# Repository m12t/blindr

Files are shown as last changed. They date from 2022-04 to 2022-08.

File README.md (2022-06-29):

# blindr
An embedded systems project that automates the articulation of window blinds such that they automatically open at sunrise and close at sunset each day.

## About the Project
The goal for this project is to have window blinds that automatically open and close around sunrise and sunset in an effort to instill healthy a sleep pattern. The code is written in C using the C/C++ SDK for the Raspberry Pi Pico microcontroller board.

The name `blindr` was a joke on the joke from this hilarious video by Joma Tech on [if Apple made window blinds...](https://youtu.be/Hv6EMd8dlQk).

## Features
1. Fully motorized articulation of blind slats
1. A generic code architecture that can be used by anyone, anywhere on Earth, without modification (_granted you use the same components found below_)
1. No bluetooth or WiFi needed -- a fully isolated and contained system
1. The ability to source latitude and longitude (needed for the solar calculations) and precise datetime data from a GNSS module
1. The ability to enable and disable automation while still being able to "manually" control the blinds via a 3 position toggle switch

## High Level Code Overview
Being an embedded system that will run 24/7, reliability and low power consumption were identified as mission-critical parameters from the project's inception.
Some examples of this in action:
1. The stepper and stepper driver board are put to sleep (no current flows to the motor or driver charge pump) whenever it's not actively running
1. The main processing cores sleep indefinitely only to be woken up by toggle switch interrupts and RTC-based alarms for solar events
1. The GNSS module is put in low power mode when it isn't needed

## User Interface
The only direct input the user has with the system is through the 3 position toggle switch. Once powered on, the Pico will wait for toggle pin input that will be used to detect the boundaries of the blinds (fully closed up and fully closed down). It's critical that the first input in either direction (the order doesn't matter) goes all the way to the desired boundary. Once low and high boundaries are set, the toggle pin can be used to control the position of the blinds "manually". The code keeps track of the position of the blinds at all times and will not let the blinds turn past the given boundaries. To disable automation and keep the blinds shut indefinitely, leave the toggle switch flipped up or down which will move to the specified boundary, sleep the stepper, and wait for the toggle to be reset to the neutral position to enable automation again. There is currently no way to leave the blinds open and disable automation without unplugging the unit. This functionality could be encoded in a switch pattern such as `[up] [down] [up]` within a specified time frame, but leaving the blinds indefinitely open wasn't nearly as useful as being able to leave them indefinitely closed.

## Hardware
There are CAD and STL files for the stepper motor housing and a driveshaft (shown below) that I drafted up for this project. They will work if you happen to have the exact model of stepper (Shinano Kenshi STP-42D201-37 with 14 tooth gear) and blinds (Home Depot Home Decorators Collection) as me. I 3D printed the mount and driveshaft in PLA, though you will likely have to design your own or find another method of getting your stepper to actually turn your blinds. There is also a housing for the Pico uC and Big Easy Driver (also shown below). This repo focuses on the code, however, which _is_ compatable with any bipolar stepper and any mounting system you might use.

Stepper housing and drive shaft:
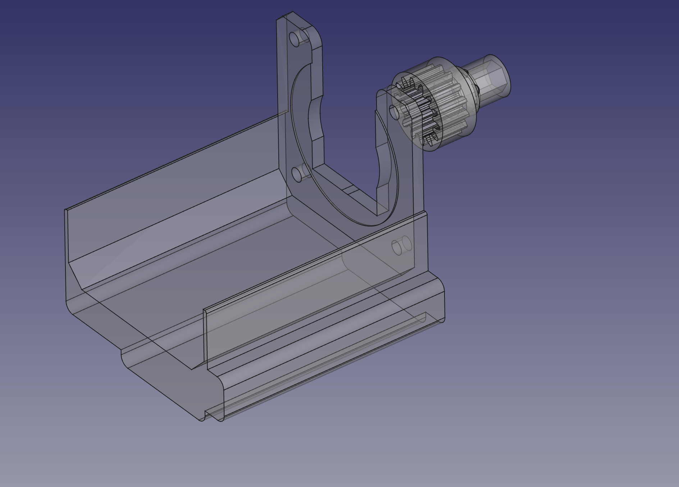
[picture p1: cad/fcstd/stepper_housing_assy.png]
Stepper housing and drive shaft


Case for the electronics:
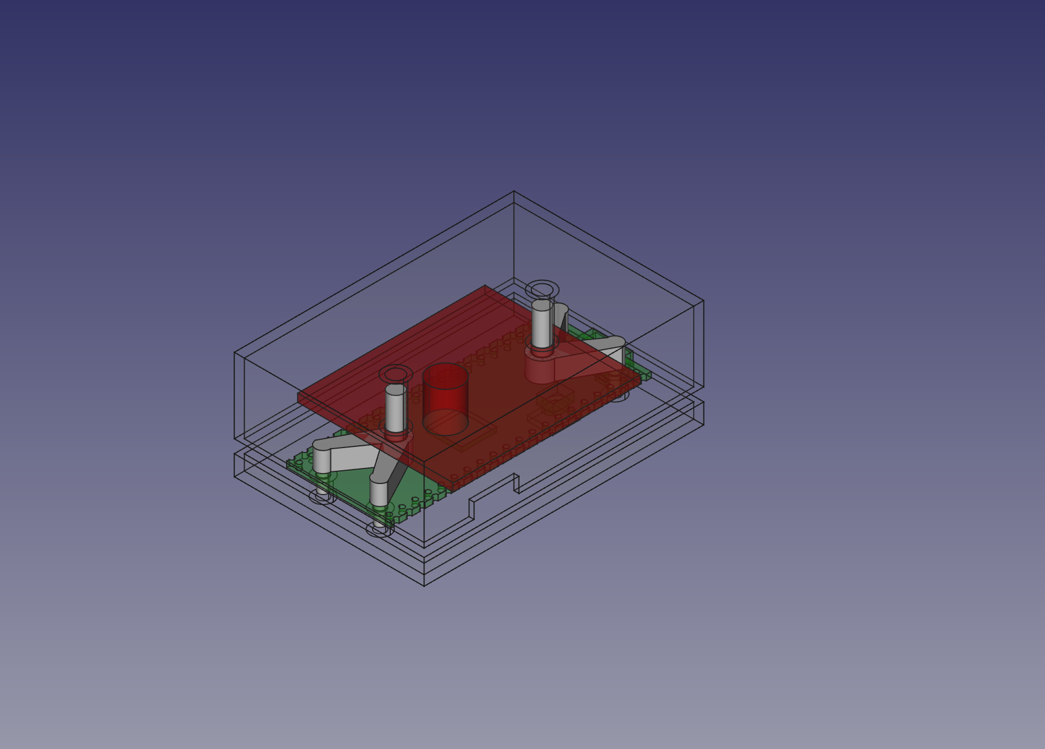
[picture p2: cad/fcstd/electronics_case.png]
Case for the electronics


# BOM (2022 prices)
1. [$4]  1x Raspberry Pi Pico
1. [$11] 1x gnss module (I used a quadcopter module - TBS M8.2 which uses a Ublox M8030-KT, though any UBX protocol module _should_ work)
1. [$21.50] 1x Big Easy Driver (A4988/A4983) capable of supplying 2A, though your particular stepper might require more or less current
1. [$15] A NEMA 17 stepper motor or similar. Smaller may work, but it needs to be bipolar. For example, a 28BYJ-48 would not work without modification
1. [FREE] old laptop charger (+8 to +30V filtered DC) which directly and indirectly powers all of the components. If you plan on building these blinds, I bet you or someone you know has an unused charger that could be repurposed to the task (**this also reduces E-waste in the process!**). As a last resort, check your local bartering site and do some haggling ;)
1. [$2] 3 position toggle switch on-off-on. Note, a momentary switch (on)-off-(on) will prevent disabling of automation with the current code since it will always trigger a rising edge when the switch resets to the center position, re-enabling automation
1. [$3] ~10 feet of thin gauge (28-30 AWG for signal wires, see your stepper's datasheet for recommended stepper wire gauge) stranded core wire
1. [$5] (optional) connectors to allow components to be easily reused for other tasks (I use Molex Picoblade, though there are certainly easier options to crimp out there)
Total: **<$60** 
I reckon that's not bad considering COTS automated blinds typically run 3-4x that and this is far more extensible and the components can be reused for other tasks!

## Contributions
1. Contributions are welcome!
1. New feature ideas, issues, PRs, etc.

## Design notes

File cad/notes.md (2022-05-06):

My naming convention for CAD files:

- `partname_xp{num}` is experimental prototype number `{num}`. eg. `faceplate_xp1`. TP is used for first attempt prototypes to test and adjust (if needed) the dimensions, geometry, or functionality of the model.
- `partname_vp{num}` is validation prototype `{num}`. VP is used for parts that are nearly complete with correct dimensions and are being tested for physical characteristics such as fit, durability, stiffness, etc.
- `partname` is a finished, validated part.

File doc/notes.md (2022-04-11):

Blindr... smart window blinds.

a real project named after the satirical YouTube video by Joma Tech `if Apple made window blinds...`

The project uses a microcontroller and a GPS module to open and close window blinds gradually around sunrise and sunset, while still allowing for manual window operation via a momentary 3 position toggle switch.

hardware:
- ✅ microcontroller (Raspberry Pi Pico)
- ✅ stepper motor (STP-42D201-37; see `/stepper.md`)
- stepper motor driver (trinamic TMC2130 or 2209)
	- form factor: module
	- chip: TMC2130
	- the TMC2130 permits 256 for virtually silent operation
	- stall detection for sensorless position finding (open and close limits on the blinds)
	- this requires a decoupling capacitor (100 uF) to the motor power supply
	- must be able to supply 1.7A peak for the stepper
- GPS module (for getting position data AND time data)
	- this eliminates the need for an RTC module because GPS provides time data
	- this also allows this code to be used by anyone on Earth as-is
	- Intuitively, blinds go on windows which look outside, so signal strength should be strong
- 3 position momentary toggle switch for manually controlling the blinds
- 5V power supply (used by Pico)
- stepper power supply
- 3D printed housing for the unit

GPS Module requirements:
- cost effective
	- high precision is not needed
- low power consumption
	- low update rate is acceptible since the Pico has an onboard RTC that can be trusted in between updates
	- best if it can be shut down and turned on as needed by the pico. Is it as simple as powering it off the pico and pulling the GPS module to ground?

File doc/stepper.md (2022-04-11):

# Exact stepper motor used in the build:

Manufacturer: Shinano Kenshi
NEMA size: 17
Mfg Part Num: STP-42D201-37
Unit cost: ~$5

## Motor Specs:
Voltage: 12V
Current: 1.7A
Holding Torque: 3.2 kg-cm

## Other notes:
Motor includes brass pinion gear, 0.50" Dia., 14 teeth, 2.23 mm pitch

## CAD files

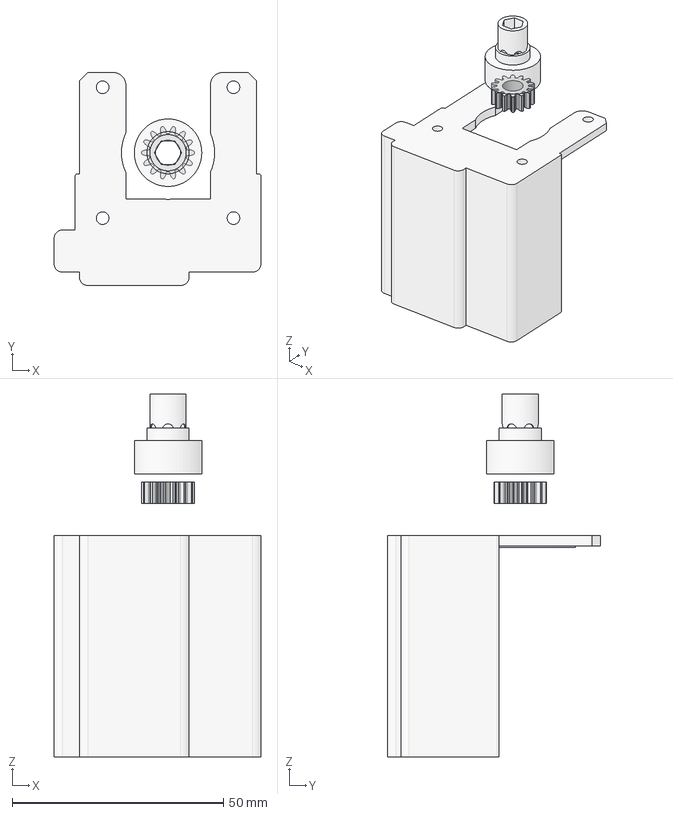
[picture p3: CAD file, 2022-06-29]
cad/fcstd/stepper_housing_assy.FCStd
49.0 x 50.5 x 86.0 mm
stepper_gear
drive_shaft
motor_mount

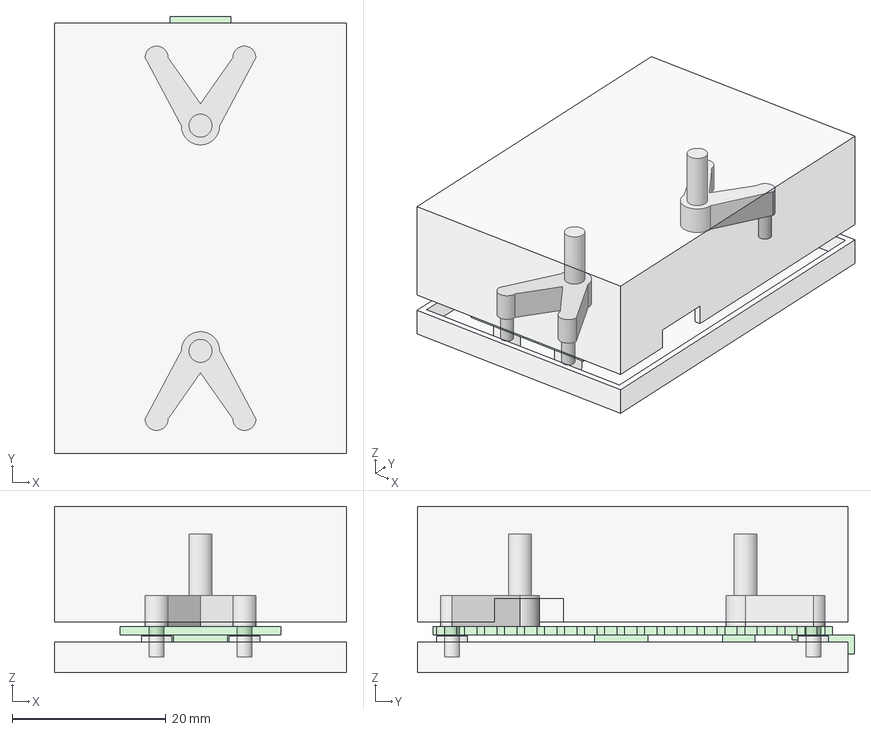
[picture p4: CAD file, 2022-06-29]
cad/fcstd/electronics_case.FCStd
38.0 x 56.8 x 21.6 mm
pico
BED
strut
strut2
case_top
case_bottom

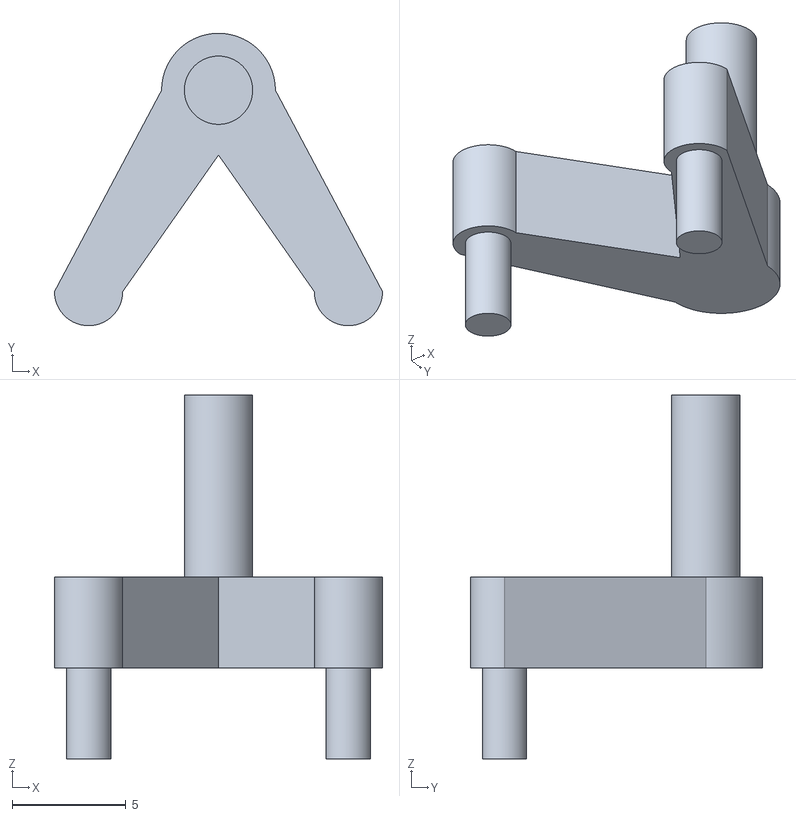
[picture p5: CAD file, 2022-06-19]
cad/meshes/strut_mesh.stl
14.4 x 12.9 x 16.0

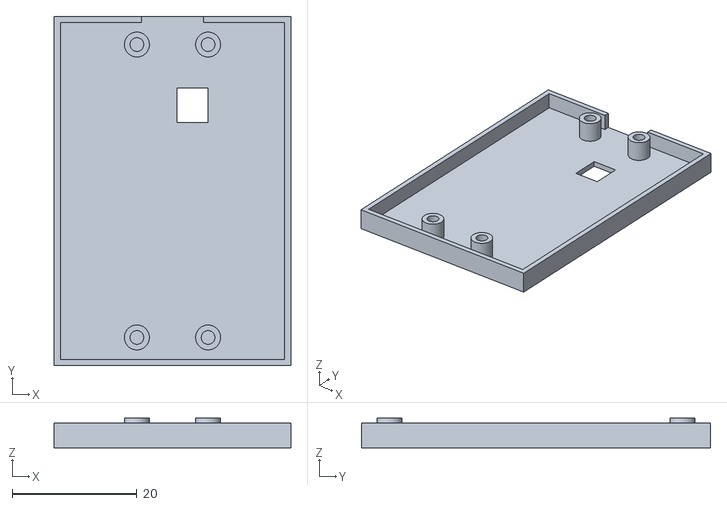
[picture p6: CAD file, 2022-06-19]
cad/meshes/case_bottom_mesh.stl
38.0 x 56.0 x 4.75

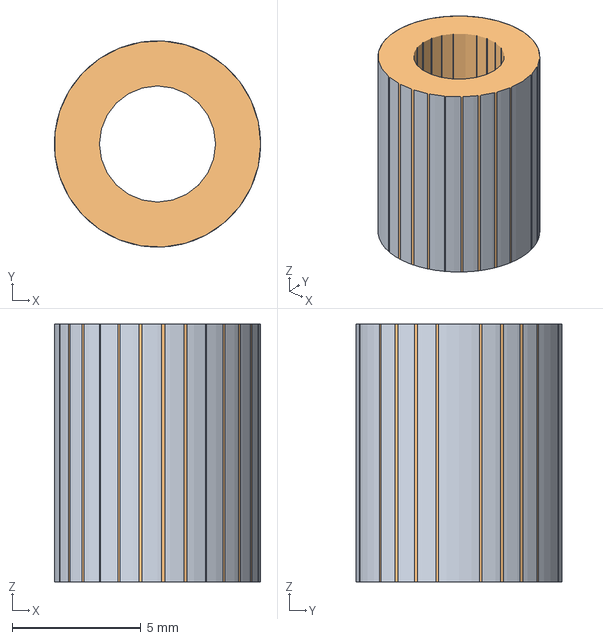
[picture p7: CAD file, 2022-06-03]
cad/fcstd/spacers.FCStd
8.00 x 8.00 x 10.0 mm
Body (Meshed)

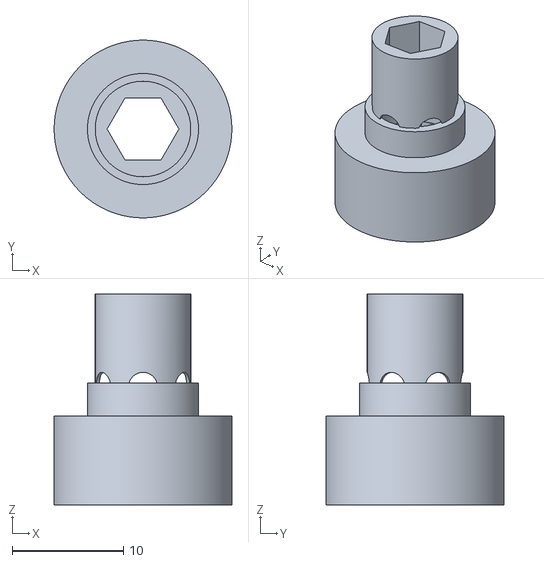
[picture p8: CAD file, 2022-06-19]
cad/meshes/sacrificial_drive_shaft.stl
16.0 x 16.0 x 19.0

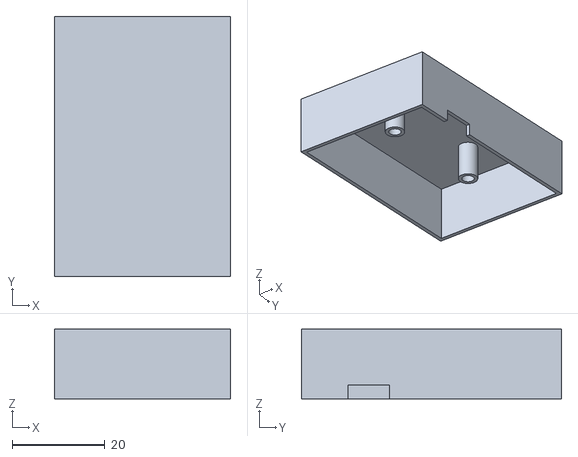
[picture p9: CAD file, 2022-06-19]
cad/meshes/case_top_mesh.stl
38.0 x 56.0 x 15.0

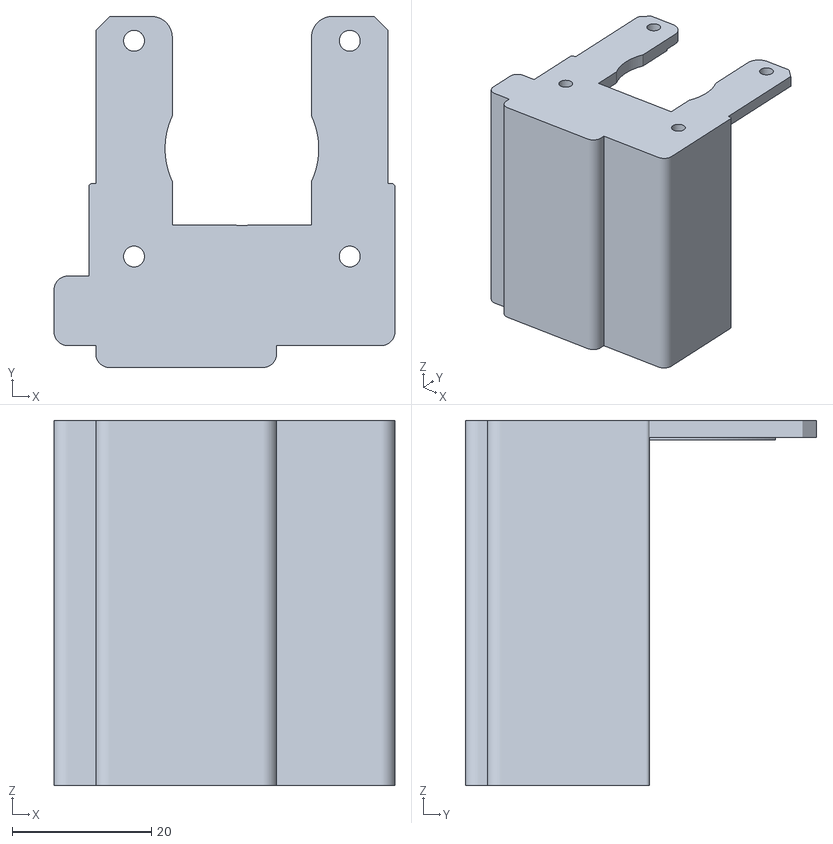
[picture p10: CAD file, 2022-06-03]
cad/meshes/motor_mount.stl
49.0 x 50.5 x 52.4

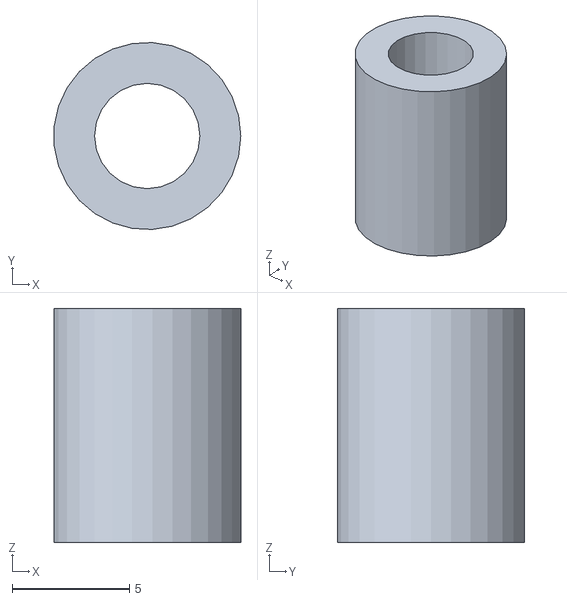
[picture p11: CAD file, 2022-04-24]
cad/meshes/window_mount_spacers_mesh.stl
7.98 x 7.99 x 10.0

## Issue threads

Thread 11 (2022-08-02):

Reduce the speed at which the blinds automatically actuate

m12t, 2022-08-02:
Increase the sleep time between steps of the motor such that the blinds gradually open and close to reduce noise of the stepper, which can be quite startling.

Closed 2022-08-02.

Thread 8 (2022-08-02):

Alternate closing the blinds up and down instead of always down

m12t, 2022-08-02:
The current process for closing the blinds automatically at sunset will close the slats in the down position every sunset. If no manual inputs are given and automation is kept enabled, the blinds will cycle through: `down ... open ... jmp` indefinitely. This can lead to subtle drift in the blinds position tracking due to mechanical "bounce back" of the blinds when the stepper motor is deactivated and no longer holding the blinds fully shut where they will spring back to slightly less firmly shut (which can't be tracked by the stepper's position counter). Cycling from lower to upper bounds should help to reduce this side effect. A simple implementation is as follows:

```c
// in blindr.c

// global var definition
uint boundary_dir = 0;  // boundary direction: 0 is down, 1 is up

// ...

// in read_actuate_alarm_sequence()
if (*solar_event == 0) {
    // ... other existing code
    boundary_dir = !boundary_dir;
}

// ...

// in actuate()
if (solar_event == 0) {
    // ... other existing code
    step_to_position(&current_position, boundary_dir*boundary_high, boundary_high);
}
```

Closed 2022-08-02.

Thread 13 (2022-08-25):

Functionality to keep the blinds open indefinitely

m12t, 2022-08-25:
Currently, automation can only be turned off by fully closing the blinds (either up or down) and leaving the toggle switch thrown in the direction the blinds are closed. There is no way to prevent the blinds from being shut at sunset. A solution would be to set a soft stop at the midpoint of the blinds range such that if you are actuating the blinds with the toggle switch, the blinds will stop in the middle until you lift the toggle switch back to neutral, and then flip the switch again to "step over" the stop in the middle. If you simply flipped the switch down and left it there, the blinds would stop in the middle position and the toggle switch would be still activated (pulling the logic to ground) thus automation could be disabled at this stage with the blinds remaining open.

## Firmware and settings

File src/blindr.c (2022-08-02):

#include "blindr.h"

// global vars
uint alarm_detected=1;  // flag that gets set by the alarm callback to cause a runthrough of the gnss read, blind actuation, and next alarm setting sequence.
uint boundary_dir=0, low_boundary_set=0, high_boundary_set=0;  // flags for direction and whether the respective boundary is set or not
int boundary_low=0, boundary_high=0, current_position=0;  // stepper positioning
uint automation_enabled = 0;  // flag useful for whether or not to operate the blinds automatically.

int main(void) {
    // -------------------------------- initialize main program vars --------------------------------

    // gnss variables
    double latitude=0.0, longitude=0.0;
    int north=-1, east=-1;
    int utc_offset;
    uint baud_rate=9600, new_baud=115200, gnss_configured=0, consec_conn_failures=0, data_found=0, time_only=0, config_gnss=1;
    int solar_event = -1;       // flag for what the next solar_event is: 0=sunset, 1=sunrise, -1=NULL/Invalid

    // -------------------------------- initialize the stepper and toggle switch --------------------------------
    // stdio_init_all();  // rbf - used for debugging
    // printf("blindr initializing...\n");
    stepper_init();
    toggle_init(&toggle_callback);

    // -------------------------------- run the main program loop indefinitely --------------------------------
    while (1) {
        // keep the program alive indefinitely while listening for interrupts and handling them accordingly.
        if (alarm_detected) {
            alarm_detected = 0;
            // printf("alarm caught!\n");
            read_actuate_alarm_sequence(&solar_event, &latitude, &longitude, &north, &east,
                                        &utc_offset, &baud_rate, new_baud, &gnss_configured, &config_gnss,
                                        &consec_conn_failures, &data_found, &time_only);
        }
        sleep_ms(30000);  // sleep for 30 seconds. Being 30s late to a solar event is acceptable. Toggle IRQs are immediate.
    }
}


void alarm_callback(void) {
    rtc_disable_alarm();
    alarm_detected = 1;
}


void toggle_callback(uint gpio, uint32_t event) {
    // * unfortunately, this callback has to contain the toggle logic instead of simply
    //   setting a flag that's caught in the main loop like alarm_callback(). The reason
    //   is so that toggle can run concurrently with the gnss module. Otherwise,
    //   it would be blocked by read_actuate_alarm_sequence()
    disable_all_interrupts_for(gpio);  // prevent further irqs while handling this one
    busy_wait_ms(100);    // combat switch bounce.

    if (event == 0x04) {
        // Falling edge detected. disable all interrupts until done
        if (!low_boundary_set || !high_boundary_set) {
            find_boundary(gpio);
        } else {
            step_indefinitely(&current_position, boundary_high, gpio);
        }
        // by now we're done with the falling action whether it's because
        // we reached a boundary of the blinds or because of a rising edge.
        // we need to know the current state to be able to configure the next
        // interrupt. if it's still 0, this means we never reset; listen for rising edge.
        // otherwise, we are reset (check that automation is enabled) and listen on another fall.
        if (gpio_get(gpio) == 0) {
            // the pin is still low, check that automation was disabled and reenable IRQs for
            // rising edge which will happen next
            // disable_automation();
            reenable_interrupts_for(gpio, GPIO_IRQ_EDGE_RISE);
        } else {
            // the pin is high again, listen for another falling edge next
            // enable_automation();
            reenable_interrupts_for(gpio, GPIO_IRQ_EDGE_FALL);
        }
    } else if (event == 0x08) {
        // Rising edge detected
        if (gpio_get(gpio) == 1) {
            // the pin is still high, listen for a falling edge next
            reenable_interrupts_for(gpio, GPIO_IRQ_EDGE_FALL);
        }
        else {
            // rising edge detected yet the toggle is still down,
            // listen for another rising edge
            reenable_interrupts_for(gpio, GPIO_IRQ_EDGE_RISE);
        }
    } else {
        // both detected, ignore
        reenable_interrupts_for(gpio, 0x0C);
    }
    set_automation_state();  // this is idempotent, so just call it every time.
}


void actuate(int solar_event) {
    if (automation_enabled && low_boundary_set && high_boundary_set) {
        // printf("actuating the blinds automatically...\n");
        if (solar_event == 1) {
            // it's a sunrise right now... open the blinds
            step_to_position(&current_position, boundary_high/2, boundary_high);
        } else if (solar_event == 0) {
            // it's a sunset right now... close the blinds in the appropriate direction
            step_to_position(&current_position, boundary_dir * boundary_high, boundary_high);
        } else {
            // do nothing (the solar event is invalid with `-1`)
        }
    }
    // printf("current position after (potential) actuation: %d\n", current_position);
}


void read_actuate_alarm_sequence(int *solar_event, double *latitude, double *longitude,
                                 int *north, int *east, int *utc_offset, uint *baud_rate,
                                 uint new_baud, uint *gnss_configured, uint *config_gnss,
                                 uint *consec_conn_failures, uint *data_found, uint *time_only) {
    // handle the current alarm/solar_event and set the next one.
    // printf("inside of read_actuate_alarm_sequence()!\n");
    uint gnss_read_successful = 0;

    actuate(*solar_event);

    gnss_init(latitude, longitude, north, east, utc_offset, baud_rate, &gnss_read_successful,
              gnss_configured, *config_gnss, new_baud, *time_only, data_found);
    if (gnss_read_successful) {
        *time_only = 1;  // now that the first runthrough has gathered lat/long, idempotently set time_only to true for future requests.
        *config_gnss = 0;
        // printf("good read\n");
    } else {
        // * the read failed. reset UART baud to the gnss module's
        //   default and set the flag to run the configuration on the module
        // printf("unsuccessful read\n");
        consec_conn_failures += 1;
        *config_gnss = 1;
        *baud_rate = 9600;  // reset the starting baud to default so the config messages work
        uart_set_baudrate(UART_ID, *baud_rate);
    }

    datetime_t now = { 0 };    // blank datetime struct to be pupulated by get_rtc_datetime(&now) call
    rtc_get_datetime(&now);    // grab the year, month, day, dotw
    int16_t year = now.year;
    int8_t month = now.month;
    int8_t day   = now.day;
    int8_t dotw  = now.dotw;
    int8_t hour  = now.hour;
    int8_t min   = now.min;
    int8_t rise_hour, rise_minute, set_hour, set_minute;  // solar event times that are populated by `calculate_solar_events()`

    // for the consistent alarm wakeup time (8:00 AM in this case)
    uint consistent_rise = 1;  // 0 = False, use solar rise always. 1 = true, always use the set time.
    int8_t consistent_rise_hour = 8, consistent_rise_minute = 0;

    // NOTE: A weekly schedule could be implemented here that uses RTC DOTW
    //       to customize the rise and set times for each day of the week. set consistent_rise = 2 for weekends only?\

    // NOTE: a min_rise_time could also be implemented whereby the blinds will open at sunrise if possible,
    //       but no earlier than a given time, say 6:00 AM. Could also go 8 hours of sleep balanced around
    //       sunrise and sunset... lots of possibilities.

    if (*solar_event == 1) {  // it's a sunrise right now
        // printf("it's a sunrise now\n");
        calculate_solar_events(&rise_hour, &rise_minute, &set_hour, &set_minute,
                               year, month, day, *utc_offset, *latitude, *longitude);
        *solar_event = 0;  // next alarm will be sunset
        hour = set_hour;
        min = set_minute;
    } else {
        if (*solar_event == 0) {  // it's a sunset right now
            // * the next solar_event is a sunrise and will occur tomorrow. Get tomorrow's solar events:
            //   - initialize tomorrow's variables to today and send the pointers to today_is_tomorrow() which will
            //     update them as needed. Use tomorrow's date to set an alarm for either the sunrise time or 00:00
            // printf("it's a sunset now\n");
            boundary_dir = !boundary_dir;  // toggle the direction so the next close is at the other boundary
            today_is_tomorrow(&year, &month, &day, NULL, *utc_offset);  // modify the day, month (if applicable), year (if applicable) to tomorrow's dd/mm/yyyy
            dotw = get_dotw(year, month, day);  // or dotw = (dotw + 1) % 7;
            calculate_solar_events(&rise_hour, &rise_minute, &set_hour, &set_minute,
                                   year, month, day, *utc_offset, *latitude, *longitude);
            *solar_event = 1;  // next alarm will be sunrise
            set_rise_times(consistent_rise, &hour, &min, consistent_rise_hour, consistent_rise_minute, rise_hour, rise_minute);
        } else {  // solar_event == -1 meaning it's startup or the last solar_event was invalid.
            // the time is after both the sunrise and sunset (or there were neither)...
            // get the sunrise time tomorrow. In the edge case there is none (ie. high
            // latitudes around the summer solstice), sleep until 0:00 tomorrow and try again.
            // printf("it's neither a sunrise or sunset...\n");
            if (check_for_solar_events_today(year, month, day, *utc_offset, *latitude, *longitude)) {
                // there is a valid solar_event today. find the next one (if applicable)
                // printf("there are solar events today...\n");
                calculate_solar_events(&rise_hour, &rise_minute, &set_hour, &set_minute,
                                       year, month, day, *utc_offset, *latitude, *longitude);
                if (rise_hour > now.hour || (rise_hour == now.hour && rise_minute > now.min)) {
                    // the next solar event is a sunrise today.
                    // printf("it's still before the sunrise today...\n");
                    *solar_event = 1;
                    set_rise_times(consistent_rise, &hour, &min, consistent_rise_hour, consistent_rise_minute, rise_hour, rise_minute);
                } else if (set_hour > now.hour || (set_hour == now.hour && set_minute > now.min)) {
                    // the next solar event is a sunset today.
                    // printf("it's still before the sunset today...\n");
                    *solar_event = 0;
                    hour = set_hour;
                    min = set_minute;
                } else {
                    // the next event is a rise tomorrow
                    // printf("it's after both sunrise and sunset today...\n");
                    today_is_tomorrow(&year, &month, &day, NULL, *utc_offset);  // modify the day, month (if applicable), year (if applicable) to tomorrow's dd/mm/yyyy
                    dotw = get_dotw(year, month, day);  // or dotw = (dotw + 1) % 7;
                    calculate_solar_events(&rise_hour, &rise_minute, &set_hour, &set_minute,
                                           year, month, day, *utc_offset, *latitude, *longitude);
                    *solar_event = 1;
                    set_rise_times(consistent_rise, &hour, &min, consistent_rise_hour, consistent_rise_minute, rise_hour, rise_minute);
                }
            } else {
                // printf("there are NO solar events today...\n");
                *solar_event = -1;  // no valid solar_event times were found, try again first thing tomorrow morning
                hour = 00;
                min = 01;
            }
        }
    }

    // printf("next solar_event: %d\n", *solar_event);
    datetime_t next_alarm = {  // the `real` version
        .year  = year,
        .month = month,
        .day   = day,
        .dotw  = dotw,
        .hour  = hour,
        .min   = min,
        .sec   = 00
    };

    if (*consec_conn_failures < MAX_CONSEC_CONN_FAILURES) {
        // set the next alarm. else abort alarm sequence.
        utils_set_rtc_alarm(&next_alarm, &alarm_callback);
        rtc_enable_alarm();
        // printf("local time is: %d/%d/%d %d:%d:%d\n", now.month, now.day, now.year, now.hour, now.min, now.sec);  // rbf
        // printf("setting the next alarm for: %d/%d/%d %d:%d:%d\n", next_alarm.month, next_alarm.day, next_alarm.year,
        //     next_alarm.hour, next_alarm.min, next_alarm.sec);  // rbf
    }
}


void set_rise_times(uint consistent_rise, int8_t *hour, int8_t *min,
                    int8_t consistent_rise_hour, int8_t consistent_rise_minute,
                    int8_t rise_hour, int8_t rise_minute) {
    if (consistent_rise == 1) {
        *hour = consistent_rise_hour;
        *min  = consistent_rise_minute;
    } else {
        *hour = rise_hour;
        *min  = rise_minute;
    }
}


void disable_all_interrupts_for(uint gpio) {
    gpio_set_irq_enabled(gpio, GPIO_IRQ_EDGE_FALL | GPIO_IRQ_EDGE_RISE, false);  // disable further interrupts during execution to mitigate mechanical switch bounce
}


void reenable_interrupts_for(uint gpio, int event) {
    gpio_set_irq_enabled_with_callback(gpio, event, true, &toggle_callback);
}


void set_automation_state(void) {
    // read the state of the toggle gpio pins
    busy_wait_ms(250);  // eliminate mechanical switch bounce
    if (gpio_get(GPIO_TOGGLE_DOWN_PIN) == 0 || gpio_get(GPIO_TOGGLE_UP_PIN) == 0) {
        disable_automation();
    } else {
        enable_automation();
    }
}


void dance(uint sleep_time) {
    // quickly step to the boundaries. Used to provide feedback when boundaries are found
    // and optionally on gnss fix.
    uint starting_pos = current_position;
    step_to_position(&current_position, (uint)(boundary_high/2), boundary_high);
    busy_wait_ms(sleep_time);
    step_to_position(&current_position, boundary_dir * boundary_high, boundary_high);
    busy_wait_ms(sleep_time);
    boundary_dir = !boundary_dir;  // toggle the direction so the next close is at the other boundary
    step_to_position(&current_position, boundary_dir * boundary_high, boundary_high);
    busy_wait_ms(sleep_time);
    step_to_position(&current_position, (uint)(boundary_high/2), boundary_high);
    busy_wait_ms(2 * sleep_time);
    step_to_position(&current_position, starting_pos, boundary_high);
}


void normalize_boundaries(void) {
    // printf("normalizing...\n");  // rbf
    // printf("current pos before: %d\n", current_position);  // rbf
    // printf("--------------\n");  // rbf
    // printf("before: %d to %d\n", boundary_low, boundary_high);
    boundary_high -= boundary_low;
    current_position -= boundary_low;
    boundary_low = 0;
    // printf("new low boundary: %d\n", boundary_low);  // rbf
    // printf("new high boundary: %d\n", boundary_high);  // rbf
    // printf("current pos after: %d\n", current_position);  // rbf
    dance(100);  // confirm boundaries are set
}


void find_boundary(uint gpio) {
    // printf("finding boundary\n");
    // wait for down toggle
    busy_wait_ms(100);  // combar switch bounce
    int stepped = 0;
    // printf("gpio: %d\n", gpio);
    uint dir = gpio == GPIO_TOGGLE_UP_PIN ? 0 : 1;
    // printf("dir: %d\n", dir);
    wake_stepper();
    while (gpio_get(gpio) == 0) {
        // printf("stepping\n");
        // while the switch is still pressed
        single_step(&current_position, dir, 1500);
        stepped = 1;
    }
    sleep_stepper();
    // update the respective boundary
    if (stepped && dir == 0) {
        // printf("stepped in dir 0\n");
        boundary_high = current_position;
        high_boundary_set = 1;
        // printf("Upper boundary found: %d\n", boundary_high);  // rbf
    } else if (stepped && dir == 1) {
        // printf("stepped in dir 1\n");
        boundary_low = current_position;
        low_boundary_set = 1;
        // printf("Lower boundary found: %d\n", boundary_low);  // rbf
    } else {
        // was just switch bounce, ignore it.
    }
    // printf("low_boundary_set: %d, high_boundary_set: %d\n", low_boundary_set, high_boundary_set);
    if (low_boundary_set && high_boundary_set) {
        normalize_boundaries();
    }
}


void enable_automation(void) {
    automation_enabled = 1;
    // printf("automation state: %d\n", automation_enabled);  // rbf
}


void disable_automation(void) {
    automation_enabled = 0;
    // printf("automation state: %d\n", automation_enabled);  // rbf
}

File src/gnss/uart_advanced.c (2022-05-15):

/**
 * Copyright (c) 2020 Raspberry Pi (Trading) Ltd.
 *
 * SPDX-License-Identifier: BSD-3-Clause
 */

#include <stdio.h>
#include "pico/stdlib.h"
#include "hardware/uart.h"
#include "hardware/irq.h"


/// \tag::uart_advanced[]

#define UART_ID uart1
#define BAUD_RATE 9600
#define DATA_BITS 8
#define STOP_BITS 1
#define PARITY    UART_PARITY_NONE

// We are using pins 0 and 1, but see the GPIO function select table in the
// datasheet for information on which other pins can be used.
#define UART_TX_PIN 4
#define UART_RX_PIN 5

static int chars_rxed = 0;

// RX interrupt handler
void on_uart_rx() {
    while (uart_is_readable(UART_ID)) {
        uint8_t ch = uart_getc(UART_ID);
        // Can we send it back?
        if (uart_is_writable(UART_ID)) {
            // Change it slightly first!
            printf("%c", ch);
        }
        chars_rxed++;
    }
}

void setup() {
    printf("\n\n Initializing... \n");
    stdio_init_all();
    uart_init(UART_ID, 9600);

    // Set the TX and RX pins by using the function select on the GPIO
    // Set datasheet for more information on function select
    gpio_set_function(UART_TX_PIN, GPIO_FUNC_UART);
    gpio_set_function(UART_RX_PIN, GPIO_FUNC_UART);

    // Actually, we want a different speed
    // The call will return the actual baud rate selected, which will be as close as
    // possible to that requested
    // int __unused actual = uart_set_baudrate(UART_ID, BAUD_RATE);

    // Set UART flow control CTS/RTS, we don't want these, so turn them off
    uart_set_hw_flow(UART_ID, false, false);

    // Set our data format
    uart_set_format(UART_ID, DATA_BITS, STOP_BITS, PARITY);

    // Turn off FIFO's - we want to do this character by character
    uart_set_fifo_enabled(UART_ID, false);

    // Set up a RX interrupt
    // We need to set up the handler first
    // Select correct interrupt for the UART we are using
    int UART_IRQ = UART_ID == uart0 ? UART0_IRQ : UART1_IRQ;

    // And set up and enable the interrupt handlers
    irq_set_exclusive_handler(UART_IRQ, on_uart_rx);
    irq_set_enabled(UART_IRQ, true);

    // Now enable the UART to send interrupts - RX only
    uart_set_irq_enables(UART_ID, true, false);

    // OK, all set up.
    // Lets send a basic string out, and then run a loop and wait for RX interrupts
    // The handler will count them, but also reflect the incoming data back with a slight change!
    // uart_puts(UART_ID, "\nHello, uart interrupts\n");
}


int main() {
    setup();

    while (1)
        tight_loop_contents();
}

/// \end:uart_advanced[]

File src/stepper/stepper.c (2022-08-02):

#include "stepper.h"


void stepper_init(void) {
    // printf("Initializing Stepper\n");
    gpio_init(SLEEP_PIN);
    gpio_init(STEP_PIN);
    gpio_init(DIRECTION_PIN);

    gpio_set_dir(SLEEP_PIN, GPIO_OUT);
    gpio_set_dir(STEP_PIN, GPIO_OUT);
    gpio_set_dir(DIRECTION_PIN, GPIO_OUT);

    sleep_stepper();  // default to sleeping the stepper
}


void wake_stepper() {
    gpio_put(SLEEP_PIN, 1);  // current is now flowing throught the stepper
    busy_wait_ms(2);  // per instructions, leave >1ms after sleep before step input
}


void sleep_stepper() {
    // save power and reduce heat/stress by shutting down the stepper when it isn't
    // needed since stepper motors pull full current even when stationary.
    busy_wait_ms(250);  // to combat bounce in position of the blinds when moving them really fast.
    gpio_put(SLEEP_PIN, 0);
    busy_wait_ms(2);  // purely a safety margin
}


void single_step(int *current_position, uint direction, uint sleep_time) {
    // create a single rising edge to trigger a single
    // step and update the current position accordingly
    if (direction == 0 || direction == 1) {
        gpio_put(DIRECTION_PIN, direction);
        // it's a valid direction, take a step
        gpio_put(STEP_PIN, 0);
        busy_wait_us(sleep_time);  // give a healthy margin between signals - busy wait needed during interrupt
        gpio_put(STEP_PIN, 1);
        *current_position += -(2*direction - 1);  // map [0, 1] to [-1, 1] and flip the sign since 0 is up
        // printf("single step -- dir: %d, pos: %d\n", direction, *current_position);  // rbf
    }
}


int step_indefinitely(int *current_position, int BOUNDARY_HIGH, uint toggle_pin) {
    // alternate to single_step() where this function reads the toggle switch value
    // directly and also modifies the current position automatically.
    // NOTE: this function can only be called once the boundary are already set
    //       since the startup routine automatically reads the initial toggle inputs
    //       as setting the lower and upper boundaries (in no particular order)
    // printf("stepping indefinitely...\n");
    wake_stepper();
    uint direction = toggle_pin == GPIO_TOGGLE_UP_PIN ? 0 : 1;  // change to whatever pin ends up being used...
    while ((gpio_get(toggle_pin) == 0) &&
           (*current_position <= BOUNDARY_HIGH) &&
           (*current_position >= 0)) {
        // the pin is still pulled high and the position is within the range, steep
        if ((*current_position >= BOUNDARY_HIGH && direction == 0) ||
            (*current_position <= 0 && direction == 1)) {
            // the current position is at a boundary and the direction is trying
            // to move it out of bounds. Disallow and exit the loop.
            break;
        } else {
            // a valid step can be taken, do so:
            single_step(current_position, direction, 1500);
        }
    }
    sleep_stepper();
}


int step_to_position(int *current_position, int desired_position, int BOUNDARY_HIGH) {
    // receive the current position, desired_position, and high boundary (low boundary is normalized to 0)
    // and step to the desired destination, updating the current position pointer along the way
    // return 0 for no action taken, 1 for step(s) were performed. It's not necessary to return the number
    // or net number of steps taken as *current_position is updated each step here.

    // check that the inputs are valid
    if ((desired_position < 0) ||
        (desired_position > BOUNDARY_HIGH) ||
        (desired_position == *current_position)) {
        // invalid input or no movement necessary
        return 1;  // no steps taken
    }

    wake_stepper();
    uint direction;

    while (*current_position != desired_position) {
        // printf("stepping to position\n");
        direction = *current_position > desired_position ? 1 : 0;  // change this to whatever ends up being up and down on the blinds
        single_step(current_position, direction, 4000);  // roughly 1500 steps from midpoint to boundary, (6 second desired transit time) / 1500 => 4000us per step
    }

    sleep_stepper();
    return 0;
}

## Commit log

2022-04-09 added preliminary solar.c and notes on stepper drivers
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2022-04-12 added window plug cad file
    [window_blind_plug.FCStd]
2022-04-12 added dirs for sliced gcode and stl files within the cad dir
    [window_blind_plug_mesh.stl]
2022-04-12 added dir for slices (.3mf files)
    [window_blind_plug_mesh.3mf]
2022-04-16 added stepper motor gear
    [stepper_housing.FCStd]
2022-04-16 added toggle switch body
    [stepper_housing.FCStd, toggle_switch_housing.FCStd]
2022-04-18 added pico pinout and some cad file mods
    [blind_channel.FCStd, toggle_switch_housing.FCStd]
2022-04-23 made the drive shaft in CAD connecting stepper and blinds
    [mod_point8.3mf, mod_point8.stl, mod_point85.stl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]
2022-04-23 added stl and gcode for the drive shaft
    [drive_shaft.3mf, drive_shaft.stl, mod_point8.3mf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]
2022-04-23 shortened the drive shaft to allow the stepper to fit within the frame
    [drive_shaft.3mf, drive_shaft.stl, stepper_housing.FCStd]
2022-04-24 added 10mm spacers to go on the mounting brackets for the blinds. Using a direct drive shaft, the stepper was too tall to mount the blinds. These spacers were the easiest and fastest solution. There 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
    [gears.FCStd, spacers-Body (Meshed).stl, spacers.FCStd]
2022-04-24 finished spacers to give clearance for stepper motor within the blind channel.
    [16_spacers.3mf, spacers.FCStd]
2022-05-06 rough sketched stepper motor faceplate
    [stepper_housing.FCStd]
2022-05-06 first prototype slices and meshes.
    [drive_shaft.stl, mod_point8.stl, mod_point85.stl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]
2022-05-06 made changes to stepper faceplate mount based on the first printed prototype
    [motor_faceplate003_mesh.stl, motor_faceplate_vp2_mesh.3mf, motor_faceplate_vp2_mesh.stl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]
2022-05-06 added my helper notes on versioning cad files
2022-05-06 modified stepper faceplate to have wider screw head holes and the correct depth for m3x10 screws
    [stepper_housing.FCStd, window_mount_spacers_mesh.stl]
2022-05-11 final validation prototype of stepper faceplate mount and some rearrangements of files
    [motor_faceplate003_mesh.3mf, motor_faceplate_vp2_mesh.3mf, motor_faceplate_vp3_mesh.3mf]
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2022-05-13 got sleep working for the stepper and upped the speed of the motor to 60us sleep per step
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2022-05-14 added comment on GPIO pin usage for stepper.c
2022-05-14 stopped tracking gcode and slicer files
    [16_spacers.3mf, drive_shaft.3mf, motor_faceplate_vp3_mesh.3mf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]
2022-05-15 read some output (illegible) from the GPS via UART in c
2022-05-15 successfully read GPS data over uart (by setting STOP_BITS to `1`)
2022-05-17 added a flag for printing to console or not
2022-05-17 started using `uart_read_blocking()` to read the NMEA data at once
2022-05-18 split NMEA lines on `\r\n` carriage return and line feed chars denoting the end of a sentence
2022-05-20 small loop to interate through sentences and print all valid ones. this can be used to further parse useful sentences such as GGA or VTG identifiers
2022-05-20 added header file and moves function prototypes there
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2022-05-22 changed default uart init baud rate to 115200 from 9600 to match the newly changed gnss module default baud rate
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2022-05-22 got setup running without the buffer (which is for console printing and unnecessary for the final system)
2022-05-25 solved bug in `parse_gga` where I was assigning to the pointer not its value
    [gnss.c]
2022-05-25 solved bug when parting lat and long
    [gnss.c]
2022-05-25 fixed the direction to negative value. works now.
    [gnss.c]
2022-05-25 refactored output to show both ZDA and GGA messages are being parsed correctly
    [gnss.c]
2022-05-25 fixed bug where missing cast of (int)*position caused the same position to be subtracted from itself instead of subtracting only the integer value which leaves the trailing digits
    [gnss.c]
2022-05-25 added a variable for tracking position fix quality from the GGA message. this is useful on startup for validating the coordinates and the time before saving the values
    [gnss.c]
2022-05-26 debugged issue on startup when waiting for gnss signal a hardfault would trigger and crash the program. the solution is that the pointer array `sentences` had junk values as it was not initialized to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
    [gnss.c]
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2022-05-28 added checking if gpio direction pin is already set to the correct direction, leave it be instead of writing another put
    [blindr.c, stepper.c]
2022-05-28 removed calls to wake_stepper() and sleep_stepper() within the single_step() function to reduce stress on the stepper driver. the respective wake and sleep calls must be made around the loop that cal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
2022-05-28 refactored to handle toggle input in `stepper.c`. Also added a function for actually creating the rising edge to trigger a step to make code more DRY
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2022-05-31 added patch for when the blind position hit a boundary it would stop prevent all stepping, even in the valid direction
    [blindr.c, stepper.c]
2022-05-31 added defines for toggle pin numebers (not permanent) and added sett_automation_status() function to check the pin state after an interrupt to set the automation status.
2022-05-31 updated tasklist, added a speed parameter for stepper single_step() so the intial boundary finding can be more precise
2022-05-31 added (untested) formula for calculating DOTW. Also added logit to de-initialize the uart once the RTC is set and positional data are established
2022-06-01 some bug fixes to utils.c
    [gnss.c]
2022-06-02 this build compiles with the solar functions. also fixed the bug of utc offset being set before longitude and the bug of utc_offset being incorrectly cast as uint8_t instead of int8_t, which is of co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
    [blindr.c, gnss.c, stepper.c]
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2022-06-02 testing moving the stepper with the toggle and edge detection. patched bug whereby the direction was reversed
    [blindr.c, stepper.c]
2022-06-02 modified the drive shaft to be sacrificial and to shear off should the stepper hit a boundary and continue to apply torque that may permanently damage the blinds.
    [stepper_housing.FCStd]
2022-06-02 deleted the faceplate and integrated it into a new one-piece housing
    [drive_shaft_vp1_mesh.stl, motor_faceplate2_xp1_mesh.stl, motor_mount_xp1_mesh.stl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]
2022-06-03 cad changes
    [drive_shaft_mesh_10.stl, motor_mount_vp002_10.stl, stepper_housing.FCStd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]
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2022-06-03 wired up the blinds and had a bug. turned back on stdio. ultimately the crimp on one of the toggle switch wires was faulty. the code was fine.
    [blindr.c, toggle.c]
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2022-06-03 commented out printf() statements, increase stepper sleep times accordingly (printf()s add latency that made a 250us sleep time with print act like ~500us without).
2022-06-03 Cleaned up CAD files
    [blind_channel.FCStd, drive_shaft.stl, drive_shaft_mesh_10.stl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]
2022-06-04 refactored set_next_alarm() to be more tolerant of drift in the Pico`s RTC
    [blindr.c]
2022-06-04 bug patches and refactored code to power on/off gnss module to recalibrate the onboard RTC twice daily
    [blindr.c, gnss.c]
2022-06-05 added logic to timeout on a gnss connection and refactored the reading of uart to be non-blocking
2022-06-05 fixed bug of spammed messages after sleeping the gnss and deinitializing uart. patch: disable IRQs but do not disable uart
    [gnss.c]
2022-06-05 replaced gnss_found variable with a check on the contents of buffer[0] which frees up parse_buffer() for all subsequent runs where it will unnecessarily declare gnss_found = 1
    [blindr.c, gnss.c]
2022-06-15 refactored code to use PIO and DMA to listen to the gnss over UART and leave the two cores free
2022-06-15 patched `NO PROGRAM SPACE` pio bug
    [gnss.c]
2022-06-16 debugged the issue of gnss signals only being picked up once... it was the sleeping/waking of the gnss. try again without multicore
    [blindr.c, gnss.c]
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2022-06-17 refactored the read actuate alarm sequence function to better handle errors and be more DRY
    [blindr.c, gnss.c]
2022-06-17 removed all printf()s, commented out all RBFs and compiled for release without debug info
2022-06-18 added electronics housing and other CAD components
    [case_bottom_mesh.stl, case_top_mesh.stl, electronics_case.FCStd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]
2022-06-19 cad changes and some bug fixes
    [case_bottom_mesh.stl, case_top_mesh.stl, electronics_case.FCStd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]
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2022-06-20 increased timeout for gnss fix
    [blindr.c, gnss.c, stepper.c]
2022-06-21 disabled sleeping of gnss to increase the changes of a gnss fix
    [blindr.c, gnss.c, stepper.c]
2022-06-22 added logic to explicitly enable and disable the RTC alarm when it is set and when an alarm is triggered. Also added code to temporarily disable toggle IRQ while handling RTC alarm to ensure the alar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
2022-06-23 patched dotw alarm bug
    [blindr.c, stepper.c]
2022-06-29 added cad images
    [electronics_case.FCStd, stepper_housing_assy.FCStd]
